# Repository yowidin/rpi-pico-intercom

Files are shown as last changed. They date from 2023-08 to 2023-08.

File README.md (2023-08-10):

# Intercom Switcher

Remotely-controlled intercom switcher based on a Raspberry Pi Pico and a SG90 servo motor.

**WARNING:** Do not open your intercom and fiddle around if you don't know what you are doing, even small AC voltages
may be dangerous or even fatal. Proceed (or better - don't) on your own risk.

## Power Supply

The `HTA-811` intercom I have provides ~12V AC on the door opener terminal. Using a bridge rectifier with a step-down
converter can provide the RPi Pico with enough power:

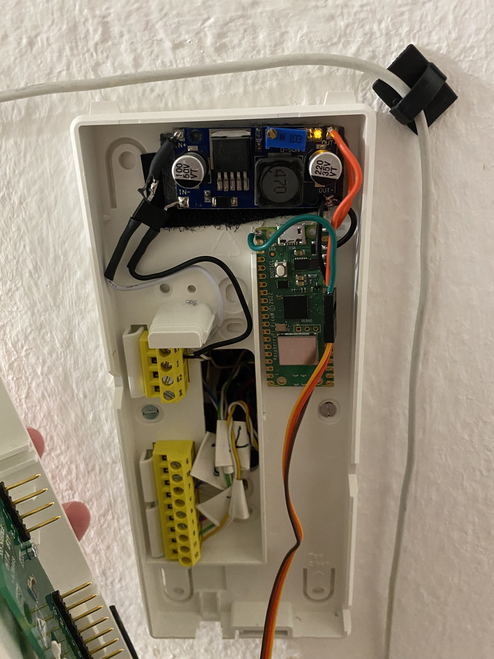
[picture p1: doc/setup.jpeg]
setup


**NOTE:** The hijacked power supply is not stable enough and results in frequent reboots during the busy hours. So I
recommend using a dedicated power supply instead.

### Servo

Depending on the target state, the servo power consumption might spike dramatically, to avoid that, the switcher first
slowly swipes through all the possible positions and then settles in the middle. When turning the intercom on/off,
the desired position is not set directly, but instead slowly changed from the current position.

## UI

If there is no configuration present, the board will spin up an access point called `RpiIntercom`, see
[wifi.py](./wifi.py) for details. After connecting to it you should be able to configure a network to connect to.

## API

See the [server.py](./server.py) file for a list of possible POST commands, and the
[scheduler](./doc/scheduler/scheduler) file, for an automation example.

## Mount

See [prints](./doc/prints) contents for the mount and the servo knob FreeCAD models.

## References

- [SSS Siedle HTA 811 - Door Phone - Notify in Ring](https://community.home-assistant.io/t/sss-siedle-hta-811-door-phone-notify-in-ring/405179)
- [Smarte Türklingel – Alte Sprechanlage smart machen](https://www.panbachi.de/smarte-tuerklingel-alte-sprechanlage-smart-machen/)

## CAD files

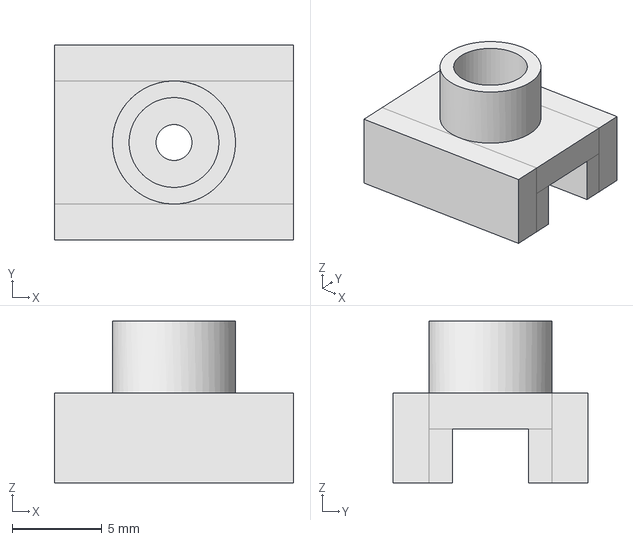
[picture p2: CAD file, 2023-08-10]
doc/prints/knob.FCStd
13.3 x 10.9 x 9.00 mm

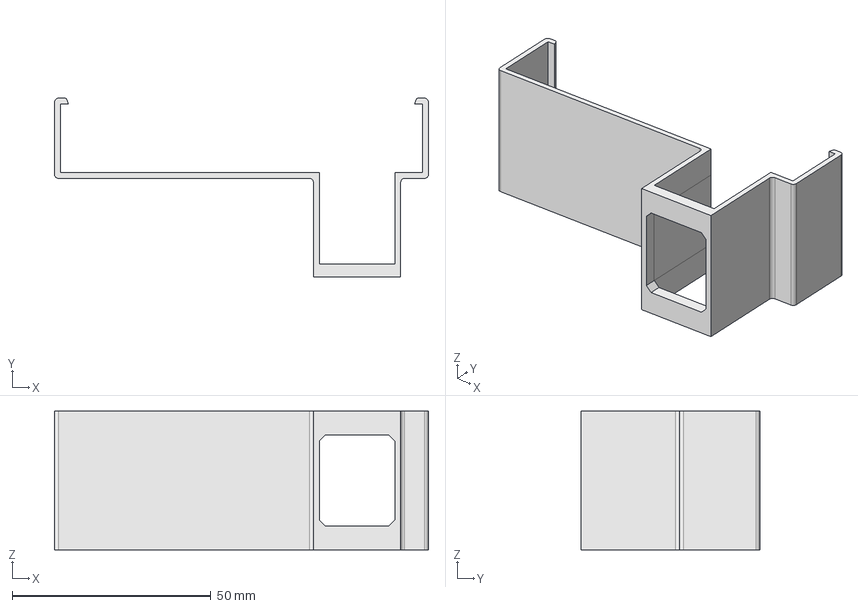
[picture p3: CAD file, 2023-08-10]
doc/prints/mount.FCStd
94.2 x 45.0 x 35.0 mm

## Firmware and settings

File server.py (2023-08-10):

import socket
import json

import os

from wifi import WiFi, USE_MOCK_WIFI
from servo import Servo

LINE_SEPARATOR = b'\r\n'


def get_file_size(path: str) -> int:
    return os.stat(path)[6]


class Stream:
    BUF_SIZE = 128

    def __init__(self, sock: socket.socket):
        self.socket = sock
        self.contents = bytearray()

    def read_some(self):
        read_buf = self.socket.recv(Stream.BUF_SIZE)
        self.contents += read_buf

    def read_until(self, token: bytes) -> bytearray:
        while True:
            idx = self.contents.find(token)
            if idx == -1:
                self.read_some()
            else:
                break

        result = self.contents[0:idx]
        self.contents = self.contents[idx + len(token):]
        return result

    def read_line(self) -> bytearray:
        return self.read_until(LINE_SEPARATOR)

    def read_exact(self, num_bytes: int) -> bytearray:
        while len(self.contents) < num_bytes:
            self.read_some()

        result = self.contents[0:num_bytes]
        self.contents = self.contents[num_bytes:]
        return result


class Request:
    def __init__(self, sock: socket.socket):
        self.stream = Stream(sock)

        request_line = self.stream.read_line()
        self.method, self.uri, self.protocol = request_line.decode('utf-8').split()
        self.headers = self._parse_headers()
        self.data = self._parse_body()

    def _parse_headers(self):
        result = {}
        while True:
            header_line = self.stream.read_line()
            if len(header_line) == 0:
                # An empty line denotes BODY start
                break

            name, value = header_line.decode('utf-8').split(': ', 1)
            result[name.lower()] = value
        return result

    def _parse_body(self):
        if 'content-length' not in self.headers:
            return None

        content_length = int(self.headers['content-length'])

        if 'content-type' not in self.headers:
            return None

        content_type = self.headers['content-type']

        if content_type != 'application/json':
            return None

        body_bytes = self.stream.read_exact(content_length)
        return json.loads(body_bytes.decode('utf-8'))

    def __str__(self):
        return f'{self.method} {self.uri}'


class Server:
    ERROR_CODE_TEMPLATE = """\
    <html>
        <head>
            <title>Error</title>
        </head>
        <body>
            <h1>%(code)d %(reason)s</h1>
        </body>
    </html>
    """

    RESPONSE_CODES = {
        200: 'OK',
        400: 'Bad Request',
        401: 'Unauthorized',
        404: 'Not Found',
        405: 'Method Not Allowed',
        500: 'Internal Server Error',
    }

    def __init__(self, request_handler, wifi: WiFi, servo: Servo, host='0.0.0.0', port=80):
        self.request_handler = request_handler
        self.wifi = wifi
        self.servo = servo

        self.host = host
        self.port = port
        self.address = self._get_bind_address()

        self.listen_socket = socket.socket()
        self.client = None
        self._listen()

    @staticmethod
    def _get_bind_address():
        ip_address_list = [x[-1] for x in socket.getaddrinfo('0.0.0.0', 80)]
        return ip_address_list[0]

    def _shutdown_current_client(self):
        try:
            if self.client is not None:
                if USE_MOCK_WIFI:
                    self.client.shutdown(socket.SHUT_RDWR)
                self.client.close()
        except Exception as e:
            print(f'Shutdown error: {e}')

        self.client = None

    def _try_sending_an_error(self):
        try:
            if self.client is not None:
                self.respond_with_error(500)
        except Exception as e:
            print(f'Error sending an error message: {e}')

    def _listen(self):
        self.listen_socket.setsockopt(socket.SOL_SOCKET, socket.SO_REUSEADDR, 1)
        self.listen_socket.bind(self.address)
        self.listen_socket.listen(1)

        while True:
            try:
                self.client, _ = self.listen_socket.accept()
                self.client.settimeout(30)
                self._handle_one()
            except Exception as e:
                print(f'Error: {e}')
                self._try_sending_an_error()
            finally:
                self._shutdown_current_client()

    def _handle_one(self):
        request = Request(self.client)
        self.request_handler(self, request)

    def _send_all(self, data: bytes):
        while len(data) != 0:
            bytes_sent = self.client.send(data)
            data = data[bytes_sent:]

    def write(self, data: bytes):
        self._send_all(data)

    def write_return_code(self, code: int):
        reason = self.RESPONSE_CODES.get(code, 'Unknown reason')
        return self.write(f"HTTP/1.1 {code} {reason}\r\n".encode())

    def write_content_type(self, content_type: str):
        return self.write(f"Content-type: {content_type}\r\n".encode())

    def write_delimiter(self):
        self.write(b'\r\n')

    def respond_with_error(self, code: int):
        self.write_return_code(code)
        self.write_content_type('text/html')
        self.write_delimiter()

        reason = self.RESPONSE_CODES.get(code, 'Unknown reason')
        message = self.ERROR_CODE_TEMPLATE % {'code': code, 'reason': reason}
        self.write(message.encode())


def handle_one_file(server: Server, path: str):
    if path.endswith('js'):
        content_type = 'text/javascript'
    elif path.endswith('css'):
        content_type = 'text/css'
    elif path.endswith('html'):
        content_type = 'text/html'
    else:
        content_type = 'text/plain'

    file_size = get_file_size(path)
    with open(path, 'r') as f:
        server.write_return_code(200)
        server.write_content_type(content_type)
        server.write(f'Content-Length: {file_size}\r\n'.encode())
        server.write_delimiter()

        buf_size = 100
        buf = f.read(buf_size)
        while len(buf) != 0:
            server.write(buf.encode())
            buf = f.read(buf_size)


def handle_scan(server: Server, _: Request):
    scan_results = server.wifi.scan()

    result = []
    for line in scan_results:
        result.append([line[0].decode('utf-8'), line[3]])

    return result


def handle_update_config(server: Server, payload: Request):
    server.wifi.update_config(payload.data['name'], payload.data['password'])
    return {}


def handle_set_state(server: Server, payload: Request):
    if payload.data['is_on']:
        server.servo.turn_on()
    else:
        server.servo.turn_off()
    return {}


def handle_get_state(server: Server, _: dict):
    is_on = server.servo.is_on()
    is_off = server.servo.is_off()
    return {'is_on': is_on, 'is_off': is_off}


def handle_get_mac(server: Server, _: dict):
    raw_mac = server.wifi.get_mac()
    return [raw_mac.hex(':')]


def handle_post(server: Server, request: Request):
    methods = {
        'scan': handle_scan,
        'config': handle_update_config,
        'set': handle_set_state,
        'get': handle_get_state,
        'mac': handle_get_mac,
    }

    path = request.uri[1:]

    if path not in methods:
        server.write_return_code(404)
        server.write_content_type('application/json')
        server.write_delimiter()
        server.write(b'{}')
    else:
        server.write_return_code(200)
        server.write_content_type('application/json')
        server.write_delimiter()

        response = methods[path](server, request)
        response_json = json.dumps(response)
        server.write(response_json.encode())


def basic_handler(server: Server, request: Request):
    print(f'Request: {request}')

    if request.method == 'POST':
        handle_post(server, request)
        return

    if request.method != 'GET':
        server.respond_with_error(400)
        return

    content_root = 'www/'

    is_connected = server.wifi.is_connected()
    if request.uri == '/':
        if is_connected:
            path = 'client.html'
        else:
            path = 'server.html'
    else:
        path = request.uri[1:]

    full_path = content_root + path
    try:
        handle_one_file(server, full_path)
    except OSError:
        server.respond_with_error(404)


def run():
    wifi = WiFi()
    servo = Servo()
    Server(basic_handler, wifi, servo)


if __name__ == '__main__':
    run()

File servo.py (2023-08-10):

try:
    from machine import PWM, Pin
    import utime

    USE_MOCK_SERVO = False
except ModuleNotFoundError:
    USE_MOCK_SERVO = True

import time
from math import fabs


class MockServo:
    def __init__(self):
        self.current_angle = 0.0

    def goto(self, angle: float):
        self.current_angle = angle
        time.sleep(1)


class PicoServo:
    def __init__(self, pin, min_duty_ns=500000, max_duty_ns=2500000, max_speed_ns=10000, min_angle=0.0,
                 max_angle=180.0):
        self.min_duty_ns = min_duty_ns
        self.max_duty_ns = max_duty_ns
        self.max_speed_ns = max_speed_ns

        self.min_angle = min_angle
        self.max_angle = max_angle
        self.mid_point = self.min_angle + (self.max_angle - self.min_angle) / 2.0

        duty_cycle_range_ns = max_duty_ns - min_duty_ns
        angle_range = max_angle - min_angle
        self.duty_ns_per_degree = duty_cycle_range_ns / angle_range

        self.pwm = PWM(pin)

        frequency_hz = 50
        self.pwm.freq(frequency_hz)
        self.transition_delay = 1.0 / frequency_hz

        self.current_angle = 0.0
        self._swipe_to_mid()

    def goto(self, angle: float):
        if angle < self.min_angle or angle > self.max_angle:
            raise RuntimeError(f'Bad angle: {angle}')

        self._travel_to_angle(angle)
        self.pwm.deinit()

    def _swipe_to_mid(self):
        # Swipe from min to max, and from max to min, to zero in the current position.
        # (the servo consumes too much current when trying to move to another point immediately, and doesn't move at
        # all)
        self.current_angle = self.min_angle
        self._travel_to_angle(self.max_angle)
        utime.sleep(0.1)
        self._travel_to_angle(self.min_angle)
        utime.sleep(0.1)
        self._travel_to_angle(self.mid_point)
        utime.sleep(0.1)
        self.pwm.deinit()

    def _degree_to_duty_ns(self, degree):
        return self.min_duty_ns + degree * self.duty_ns_per_degree

    def _duty_ns_to_degree(self, duty_ns):
        return self.min_angle + (duty_ns - self.min_duty_ns) / self.duty_ns_per_degree

    def _travel_to_angle(self, angle):
        start = int(self._degree_to_duty_ns(self.current_angle))
        stop = int(self._degree_to_duty_ns(angle))
        step = self.max_speed_ns if self.current_angle < angle else -self.max_speed_ns

        for i in range(start, stop, step):
            self.pwm.duty_ns(i)
            utime.sleep(self.transition_delay)
            self.current_angle = self._duty_ns_to_degree(i)


class Servo:
    PIN_NAME = "GPIO0"
    ON_ANGLE = 180.0
    OFF_ANGLE = 10.0

    def __init__(self):
        if USE_MOCK_SERVO:
            self.implementation = MockServo()
        else:
            self.implementation = PicoServo(Pin(Servo.PIN_NAME, Pin.OUT))

    def is_on(self):
        return fabs(self.implementation.current_angle - Servo.ON_ANGLE) < 1.0

    def is_off(self):
        return fabs(self.implementation.current_angle - Servo.OFF_ANGLE) < 1.0

    def turn_on(self):
        self.implementation.goto(Servo.ON_ANGLE)

    def turn_off(self):
        self.implementation.goto(Servo.OFF_ANGLE)

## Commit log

2023-08-10 Initial commit
    The project is functional, but the web pages are
    pretty much broken on the mobile devices
    [server.py, servo.py, wifi.py]
2023-08-10 Fix invalid HTML parsing
    [server.py]
2023-08-10 Add more connection retries
    Sometimes, the first couple of connection attempts are failing
    [wifi.py]
2023-08-10 Error handling and transport tweaking
    [server.py]
2023-08-10 Avoid spurious servo movements
    By using a smaller off-angle
    [servo.py]
2023-08-10 Better error handling
    Avoid crashes when shutting down a connection
    [server.py]
2023-08-10 Add documentation
    [knob.FCStd, mount.FCStd]
